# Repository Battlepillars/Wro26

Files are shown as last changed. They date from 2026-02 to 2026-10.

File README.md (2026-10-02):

<div align="left">

# Table of contents

<ul dir="auto">
    <li><details><summary><a href="#the-team">The team</a></summary>
        <ul dir="auto">
            <li><a href="#nils-stauff">Nils Stauff</a></li>
            <li><a href="#olivia-greilich">Olivia Greilich</a></li>
            <li><a href="#anton-wiesen">Anton Wiesen</a></li>
            <li><a href="#team-photo">Team photo</a></li>
        </ul>
        </details>
      </li>
    <li><a href="#videos-of-the-robot">Videos of the robot</a></li>
    <li><details><summary><a href="#mobility-and-mechanics">1. Mobility and mechanics</a></summary>
        <ul dir="auto">
            <li><a href="#development-goal">Development goal</a></li>
            <li><a href="#chassis-and-mechanical-structure">Chassis and mechanical structure</a>
              <ul dir="auto">
                <li><a href="#chassis-design">Chassis design</a></li>
                <li><a href="#base-deck-iteration">Base deck iteration</a></li>
                <li><a href="#chassis-structure">Chassis structure</a></li>
              </ul>
            </li>
            <li><a href="#drivetrain-concept-and-motor-selection">Drivetrain concept and motor selection</a></li>
            <li><a href="#rear-axle-and-differential">Rear axle and differential</a></li>
            <li><a href="#front-axle-and-steering">Front axle and steering</a>
              <ul dir="auto">
                <li><a href="#ackermann-condition-in-our-steering">Ackermann condition in our steering</a></li>
                <li><a href="#mechanical-precision-of-our-steering">Mechanical precision of our steering</a></li>
                <li><a href="#front-axle-rims-and-tires">Front axle rims and tires</a></li>
              </ul>
            </li>
            <li><a href="#servo-selection-and-position">Servo selection and position</a>
              <ul dir="auto">
                <li><a href="#servo-selection">Servo selection</a></li>
                <li><a href="#servo-position">Servo position</a></li>
              </ul>
            </li>
          </ul>
          </details>
        </li>
        <li><details><summary><a href="#power-and-sensors">2. Power and sensors</a></summary>
        <ul dir="auto">
            <li><a href="#concept">Concept</a></li>
            <li><a href="#electronics-setup">Electronics setup</a></li>
            <li><a href="#camera-use-of-the-camera-and-calibration">Camera: use of the camera and calibration</a>
              <ul dir="auto">
                <li><a href="#use-of-the-camera">Use of the camera</a></li>
                <li><a href="#further-development-rotating-camera-tower">Further development: rotating camera tower</a></li>
                <li><a href="#calibration-procedure">Calibration procedure</a></li>
              </ul>
            </li>
            <li><a href="#distance-sensors">Distance sensors</a>
                <ul dir="auto">
                    <li><a href="#selection-of-distance-sensors">Selection of distance sensors</a></li>
                    <li><a href="#sensor-evaluation">Sensor evaluation</a></li>
                    <li><a href="#sensor-placement-in-the-robot">Sensor placement in the robot</a></li>
                </ul>
            </li>
            <li><a href="#gyro">Gyro</a></li>
            <li><a href="#power-budget-power-supply-and-consumption">Power budget: power supply and consumption</a>
                <ul dir="auto">
                    <li><a href="#worst-case-peak-current-and-regulator-sizing">Worst-case peak current and regulator sizing</a></li>
                    <li><a href="#measured-total-power-requirement">Measured total power requirement</a></li>
                    <li><a href="#runtime-calculation">Runtime calculation</a></li>
                    <li><a href="#avoiding-deep-discharge">Avoiding deep discharge</a></li>
                    <li><a href="#voltage-supply-of-the-individual-components">Voltage supply of the individual components</a></li>
                    <li><a href="#failure-modes-in-sensors-and-power-supply">Failure modes in sensors and power supply</a></li>
                </ul>
            </li>
          </ul>
          </details>
        </li>
        <li><details><summary><a href="#software-development">3. Software development</a></summary>
        <ul dir="auto">
            <li><a href="#software-architecture">Software architecture</a></li>
            <li><a href="#threading-and-system-flow">Threading and system flow</a></li>
            <li><a href="#driving-primitives-in-drivecontrollerpy">Driving primitives in driveController.py</a></li>
            <li><a href="#opening-challenge-driving-strategy">Opening challenge driving strategy</a></li>
            <li><a href="#obstacle-challenge-driving-strategy---strategy-change">Obstacle challenge driving strategy - strategy change</a>
              <ul dir="auto">
                <li><a href="#old-strategy-scanning-while-driving">Old strategy: scanning while driving</a></li>
                <li><a href="#new-strategy-full-scan-fixed-route">New strategy: full scan, fixed route</a></li>
                <li><a href="#passing-two-obstacles-in-one-section">Passing two obstacles in one section</a></li>
                <li><a href="#parking-and-un-parking">Parking and un-parking</a></li>
              </ul>
            </li>
            <li><a href="#serial-communication-and-data-model">Serial communication and data model</a></li>
            <li><a href="#camera-processing">Camera processing</a>
              <ul dir="auto">
                <li><a href="#mask-pipeline">Mask pipeline</a></li>
              </ul>
            </li>
            <li><a href="#software-improvements">Software improvements</a></li>
          </ul>
          </details>
        </li>
        <li><details><summary><a href="#overall-robot-system-and-technical-decisions">4. Overall robot system and technical decisions</a></summary>
        <ul dir="auto">
            <li><a href="#design-constraints">Design constraints</a></li>
            <li><a href="#system-level-risks">System-level risks</a></li>
            <li><a href="#our-robot">Our robot</a></li>
            <li><a href="#technical-specifications">Technical specifications</a></li>
            <li><a href="#system-architecture">System architecture</a></li>
            <li><a href="#key-technical-decisions">Key technical decisions</a>
              <ul dir="auto">
                <li><a href="#raspberry-pi-vs-pure-microcontroller">Raspberry Pi vs. pure microcontroller</a></li>
                <li><a href="#raspberry-pi-5-vs-raspberry-pi-cm5">Raspberry Pi 5 vs. Raspberry Pi CM5</a></li>
                <li><a href="#lidar-vs-time-of-flight-sensors--control-paradigm">LiDAR vs. time-of-flight sensors / control paradigm</a></li>
                <li><a href="#camera-height-and-detection-strategy">Camera height and detection strategy</a></li>
                <li><a href="#chassis-material-pla-vs-ppa-cf">Chassis material: PLA vs. PPA-CF</a></li>
                <li><a href="#gyro-bno055-with-and-without-magnetometer-vs-bno086-without-magnetometer">Gyro: BNO055 with and without magnetometer vs. BNO086 without magnetometer</a></li>
                <li><a href="#rear-axle-ball-differential-vs-rigid-axle">Rear axle: ball differential vs. rigid axle</a></li>
                <li><a href="#tof-sensor-vl53l8cx-vs-tmf8828">ToF sensor: VL53L8CX vs. TMF8828</a></li>
              </ul>
            </li>
            <li><a href="#development-milestones">Development milestones</a></li>
          </ul>
          </details>
        </li>
        <li><details><summary><a href="#5-construction-guide">5. Construction guide</a></summary>
        <ul dir="auto">
            <li><a href="#assembly-overview">Assembly overview</a></li>
            <li><a href="#step-1-preparing-the-3d-printed-parts">Step 1: Preparing the 3D-printed parts</a></li>
            <li><a href="#step-2-lower-deck-assembly">Step 2: Lower deck assembly</a>
              <ul dir="auto">
                <li><a href="#21-drive-motor-and-rear-axle-bearings">2.1 Drive motor and rear-axle bearings</a></li>
                <li><a href="#22-front-axle--steering-knuckles">2.2 Front axle / steering knuckles</a></li>
                <li><a href="#23-rear-axle-front-wheels-and-steering-linkage">2.3 Rear axle, front wheels and steering linkage</a></li>
              </ul>
            </li>
            <li><a href="#step-3-middle-deck-assembly">Step 3: Middle deck assembly</a>
              <ul dir="auto">
                <li><a href="#31-support-bridge-and-middle-deck">3.1 Support bridge and middle deck</a></li>
                <li><a href="#32-mount-the-baseboard-and-connect-all-components">3.2 Mount the baseboard and connect all components</a></li>
              </ul>
            </li>
            <li><a href="#step-4-upper-deck--tof-sensors-and-rotating-camera-tower">Step 4: Upper deck – ToF sensors and rotating camera tower</a>
              <ul dir="auto">
                <li><a href="#41-mount-the-upper-deck">4.1 Mount the upper deck</a></li>
                <li><a href="#42-insert-the-distance-sensors">4.2 Insert the distance sensors</a></li>
                <li><a href="#43-mount-the-camera-tower-and-camera">4.3 Mount the camera tower and camera</a></li>
                <li><a href="#44-connect-the-camera-pan-servo">4.4 Connect the camera pan servo</a></li>
              </ul>
            </li>
            <li><a href="#step-5-wiring">Step 5: Wiring</a></li>
            <li><a href="#step-6-software-installation">Step 6: Software installation</a>
              <ul dir="auto">
                <li><a href="#61-prepare-raspberry-pi-os">6.1 Prepare Raspberry Pi OS</a></li>
                <li><a href="#62-install-python-libraries">6.2 Install Python libraries</a></li>
                <li><a href="#63-install-battlepillars-software">6.3 Install Battlepillars software</a></li>
                <li><a href="#64-build-compile-and-upload-to-the-controllers">6.4 Build, compile and upload to the controllers</a></li>
              </ul>
            </li>
          </ul>
          </details>
        </li>
</ul>

# **The team** 
<div align="center">
    <a href="img/teamname.jpg" target="_blank">
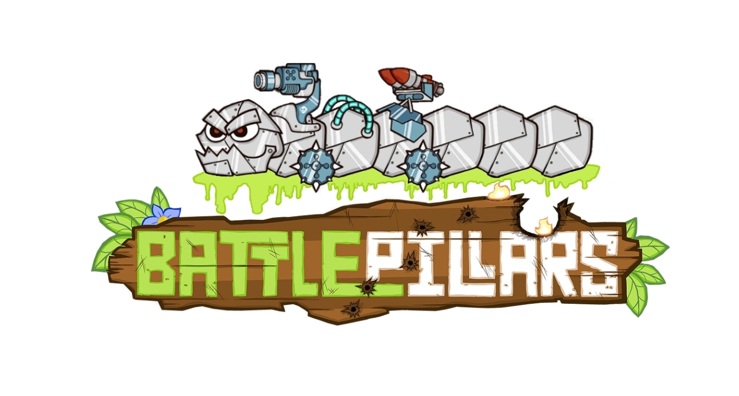
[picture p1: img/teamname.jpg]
        
    </a>
</div>
In this repository, you’ll find the documentation for the robot created by the "Battlepillars" for the 2026 World Robot Olympiad Future Engineers competition. The robot was the result of a collaborative effort by three students.

## **Nils Stauff**

<div align="center">
    <a href="img/nils.jpg" target="_blank">
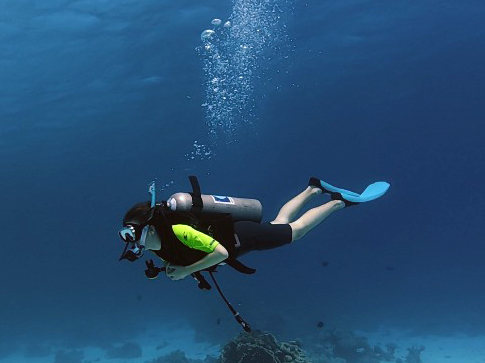
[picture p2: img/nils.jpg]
        
    </a>
</div>

Hi! I’m Nils, and I’m 17 years old. I enjoy coding and solving technical problems. In my free time, I like scuba diving and exploring the underwater world. During winter, I often go skiing, and I’m also a big fan of cats.

For our WRO project, I’m responsible for developing the robot’s software and making sure it runs as intended. It can be challenging at times, but it’s very rewarding when everything works as planned!

## **Olivia Greilich**

<div align="center">
    <a href="img/olivia.jpg" target="_blank">
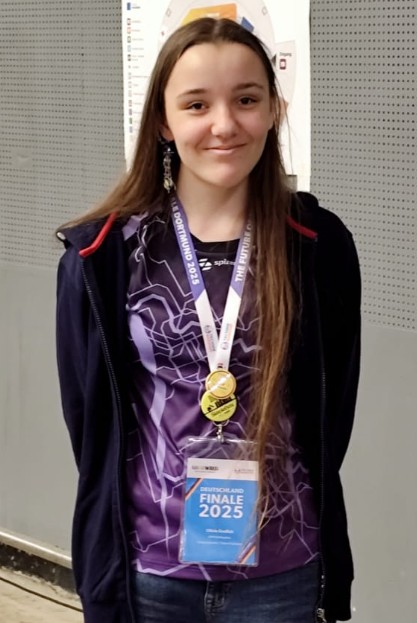
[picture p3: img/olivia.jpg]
        
    </a>
</div>

Hello everyone! My name is Olivia Greilich and I'm 17, currently attending the Lise-Meitner Gymnasium in Anrath. Languages, communicating and connecting with people is my passion, same with painting, sculpting and crocheting!
One interesting fact about me is that I am simply enamored with jellyfish of all types, colors, shapes and sizes. I have two jellyfish lamps, tons of stickers, books and of course a phone charm.
In my free time, I usually occupy myself with writing fanfiction on Archive Of Our Own (AO3).

My part of the team effort is the documentation and images you'll see below.

## **Anton Wiesen**

<div align="center">
    <a href="img/Einstellung_Lenkung.jpg" target="_blank">
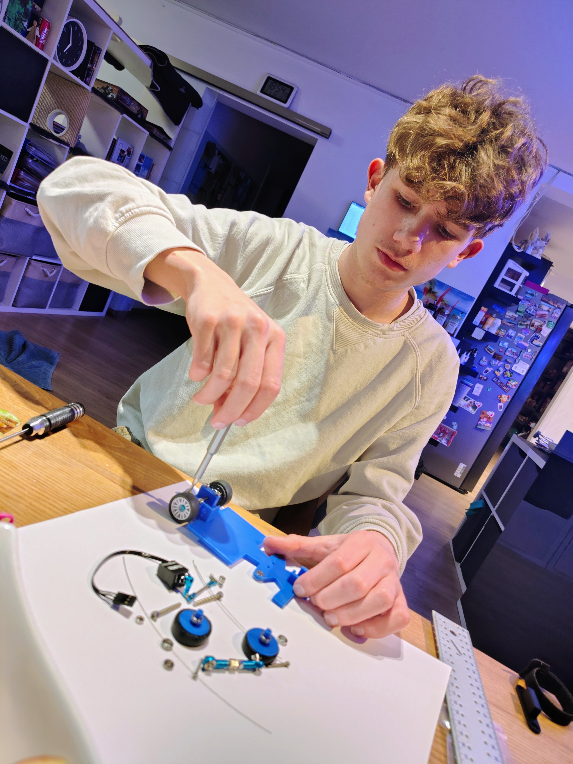
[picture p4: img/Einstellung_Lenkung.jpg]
        
    </a>
</div>

Hello! My name is Anton Wiesen, and I am 16 years old. I am responsible for the mechanical design of the robot and its technical components. My interests mainly lie in designing and building technology for robots. I am also quite experienced with 3D modelling software such as Fusion 360. In my free time, I like hanging out with friends and playing badminton at a sports club.

## **Team photo**

<div align="center">
    <a href="img/team.png" target="_blank">
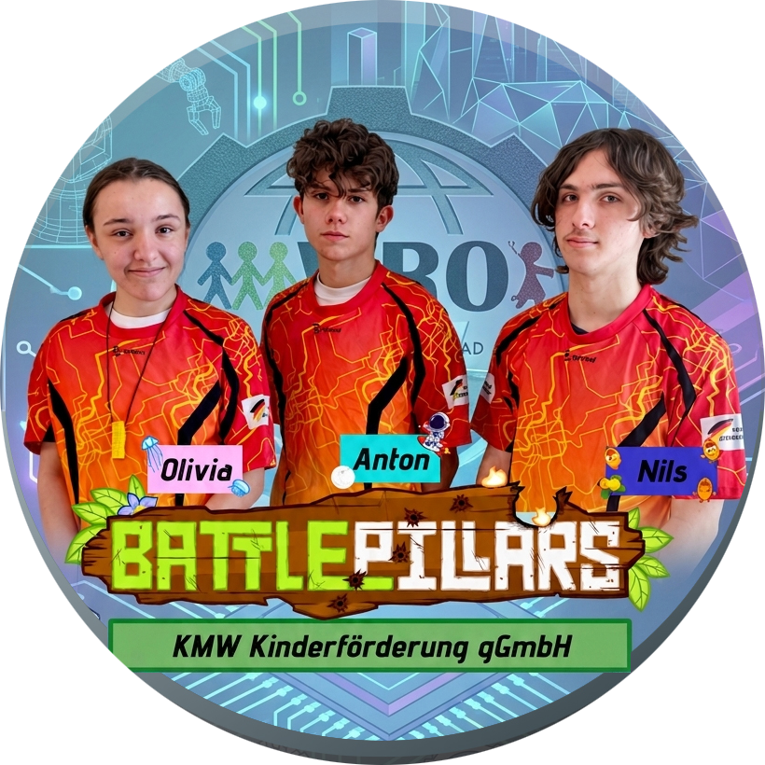
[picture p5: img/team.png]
        
    </a>
</div>
<br>

# **Videos of the robot**

The following videos show the vehicle operating autonomously, one video per run:

| Run | Link |
|---|---|
| Open Challenge | Open Challenge video (https://youtu.be/xgsjbz8JtRs?is=9g74XXmeAL3ZztfQ) |
| Obstacle Challenge | Obstacle Challenge video (https://youtu.be/dZyoW23Dgi8?is=IOlfB-I18UwgznLK) |

<br><br>

# **Mobility and mechanics**

## **Development goal**
In the 2025 season, we already successfully competed in the Future Engineers category and achieved the highest possible score in both runs at the World Final. 
<br><br>
**The goal for the 2026 season** was no longer just to reliably achieve the maximum score, but to complete the **course in the shortest possible time**. This led to three central mechanical development goals: a smaller and lighter chassis, a faster and more efficient drivetrain, and more precise steering. These goals led to a complete redesign of the chassis, drivetrain, front axle, and electronics layout.
<br><br>
The smaller form factor was meant to bring several advantages: the small size of the car allows for smaller turning radii and therefore higher agility. In addition, during the obstacle challenge, the car has more clearance to obstacles when passing through narrow sections, which makes driving more fault-tolerant and allows for higher speeds.

#### Figure 1: Comparison of the 2025 and 2026 robot designs:

<div align="center">
    <a href="img/vergleich_roboter.png" target="_blank">
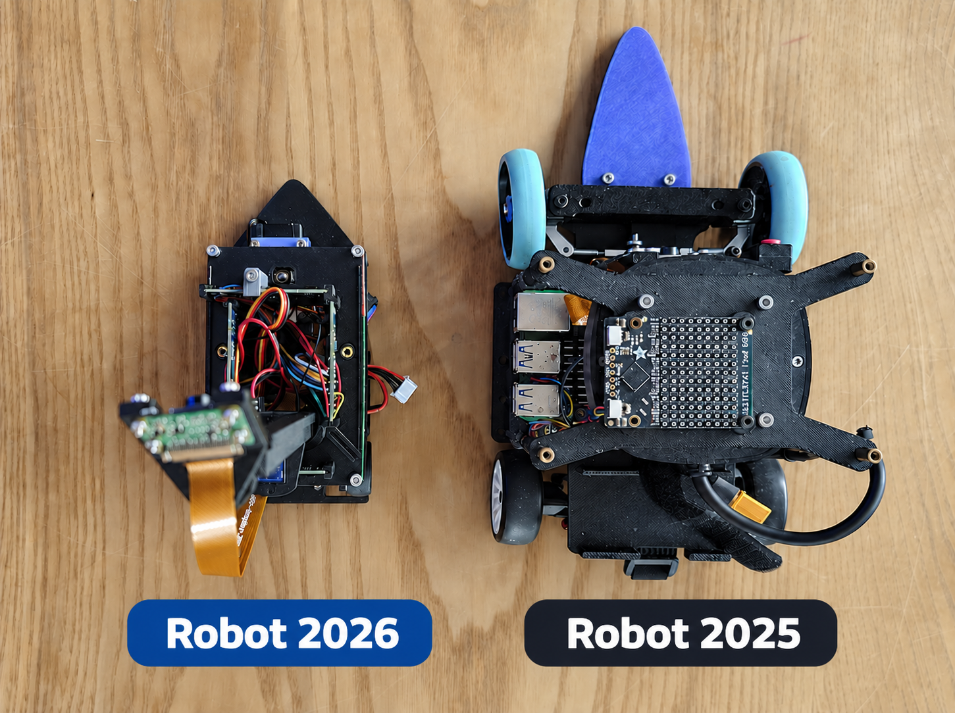
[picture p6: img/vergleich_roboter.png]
Comparison of the 2025 and 2026 robot designs
        
    </a>
</div>

<br>

## **Chassis and mechanical structure**

### **Chassis design**
The **chassis** was designed in Fusion 360. During development, **plain PLA** was used as filament since it is inexpensive and easy to print. However, the motor mount in PLA did not work reliably, since PLA creeps (deforms under constant pressure), which caused the gear backlash at the motor to drift out of tolerance.
<br><br>
In the final version, the chassis was manufactured from **PPA-CF filament**. PPA-CF is significantly stiffer and does not creep. As a result, the angles of the camera and sensors no longer change due to chassis flex. This improves the reproducibility of the sensor data and provides more consistent readings over the entire run.
<br><br>
However, this created a new problem. If the suspension was not exactly the same height on all sides, or the base deck was slightly warped, a wheel would hover slightly off the ground due to the extreme stiffness of the material and spin freely. In the previous PLA versions, this issue was compensated for by the springy properties of the material. Since we did not want to give up the positive properties of PPA-CF filament with respect to sensor data, we heated the base deck with a heat gun and carefully bent it until all wheels had good ground contact.

#### Table 1: Mechanical iterations in the chassis design:

<table align="center" border="1" style="border-collapse: collapse; border: 2px solid black; margin: 12px 0;">
  <tr>
    <th bgcolor="#4A90C2" style="border: 1px solid black; border-bottom: 3px solid black; padding: 8px; color: white;">Starting version</th>
    <th bgcolor="#4A90C2" style="border: 1px solid black; border-bottom: 3px solid black; padding: 8px; color: white;">Problem</th>
    <th bgcolor="#4A90C2" style="border: 1px solid black; border-bottom: 3px solid black; padding: 8px; color: white;">Observation before</th>
    <th bgcolor="#4A90C2" style="border: 1px solid black; border-bottom: 3px solid black; padding: 8px; color: white;">Change</th>
    <th bgcolor="#4A90C2" style="border: 1px solid black; border-bottom: 3px solid black; padding: 8px; color: white;">Observation after</th>
    <th bgcolor="#4A90C2" style="border: 1px solid black; border-bottom: 3px solid black; padding: 8px; color: white;">Decision</th>
  </tr>
  <tr>
    <td bgcolor="#EAF4FB" style="border: 1px solid black; padding: 8px;">Chassis made of PLA</td>
    <td bgcolor="#EAF4FB" style="border: 1px solid black; padding: 8px;">Motor mount deformed under continuous load, gear backlash drifted out of tolerance</td>
    <td bgcolor="#EAF4FB" style="border: 1px solid black; padding: 8px;">Backlash changed measurably after a few runs (creep), motor ran roughly</td>
    <td bgcolor="#EAF4FB" style="border: 1px solid black; padding: 8px;">Switched filament to PPA-CF</td>
    <td bgcolor="#EAF4FB" style="border: 1px solid black; padding: 8px;">Gear backlash constant, but new problem: wheel hovers slightly off the ground because base deck is too stiff</td>
    <td bgcolor="#EAF4FB" style="border: 1px solid black; padding: 8px;"><b>PPA-CF kept; new problem solved by manually rebending the base deck</b></td>
  </tr>
</table>
<br>

### **Base deck iteration**

At the start, the **base deck** consisted only of a simple rectangle. This first version served to roughly position the most important mechanical components and estimate the required footprint. The dimensions of the rear axle with ball differential, which we purchased as a pre-assembled unit with a fixed rear axle and wheel hubs, served as the initial reference point. This determined the wheelbase and thus the width of the base deck. The length of the base deck, on the other hand, was dictated by the dimensions of our self-developed PCB, since this was the largest component by area and was installed lengthwise in the chassis. For the rear axle we used a ball differential from the model-making sector, since a differential of this size is difficult to print reliably. The base deck was then gradually adapted to the actual mechanical requirements. During this process, more than fifteen versions of the base deck were created and printed until the final version was completed with all necessary cutouts, mounting points, and adaptations for the axles, wheels, sensors, and electronics. A total of ten ball bearings were used for the steering and suspension.

#### Figure 2: Iterations of the base deck:

<div align="center">
    <a href="img/iterationen_bodenplatte_eng.png" target="_blank">
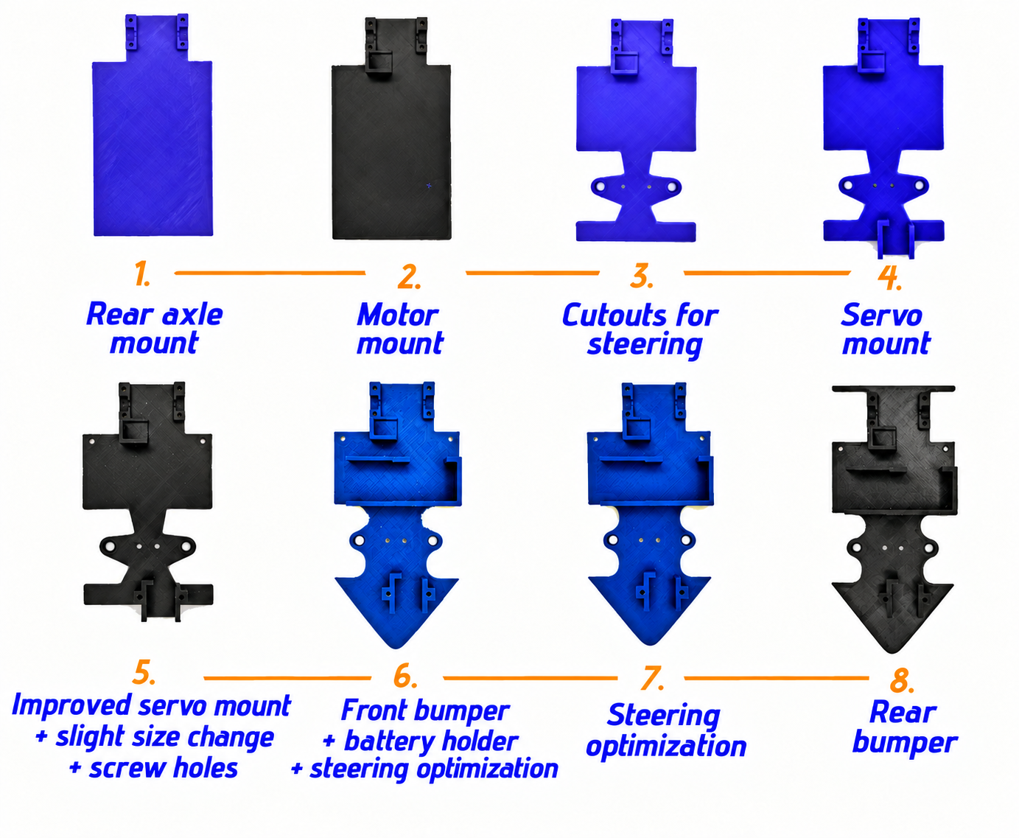
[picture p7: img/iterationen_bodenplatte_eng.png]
Iterations of the base deck
        
    </a>
</div>

### **Chassis structure**

The **chassis is split into three levels**, allowing a compact and clear integration of all components: 
<br>
<li>The base deck carries the drivetrain, battery, differential, and steering.</li>
<li>The middle deck houses the PCB, the Raspberry Pi CM5, the gyroscope, and the microcontroller.
<li>The top deck contains the camera and the ToF sensors.</li>
<br>

The finished vehicle with all components (PCB, battery, Raspberry Pi CM5, sensors, camera) has a **total weight of approx. 400 g**. 
<br>
#### Figure 3: Structure of the robot:

<div align="center">
    <a href="img/ebenen.jpg" target="_blank">
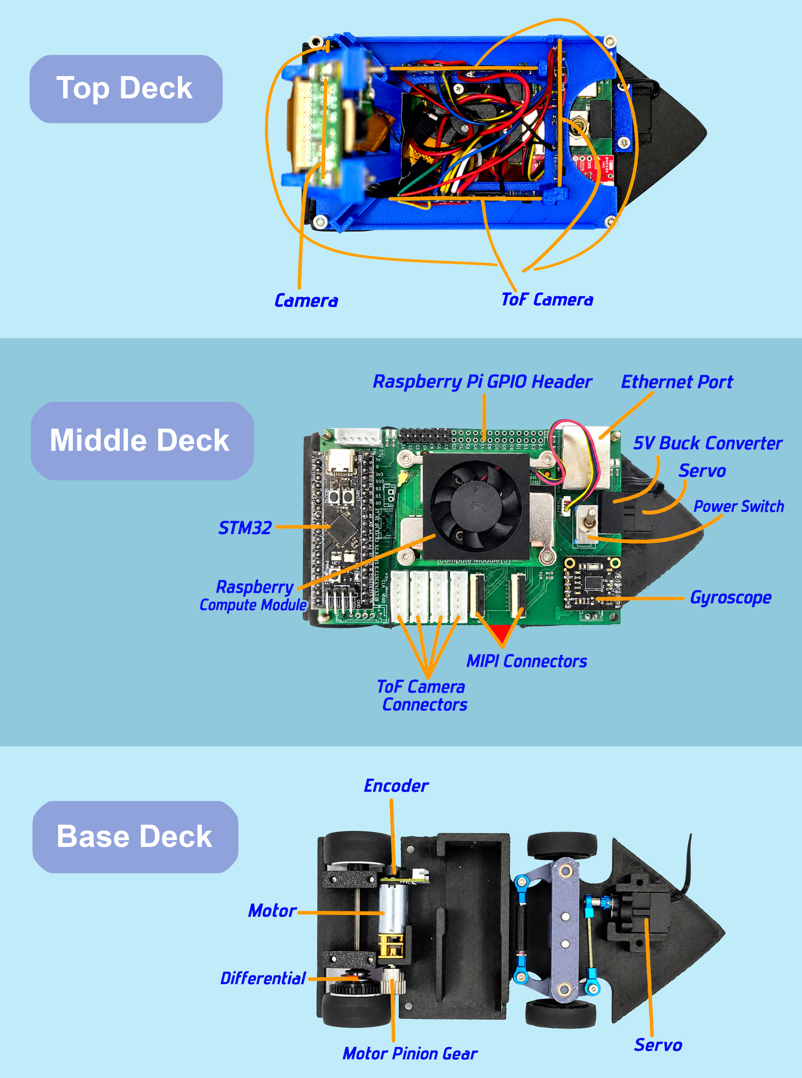
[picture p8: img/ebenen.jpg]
Three-level structure of the robot chassis
        
    </a>
</div>

## **Drivetrain concept and motor selection**

Our goal was to **drive one lap in about 10 seconds** – a race consists of three laps, which we therefore wanted to complete in about 30 seconds. The WRO track has a lap circumference (depending on the track layout) of about 8 m. This results in a required target speed of 8 m / 10 s = 0.8 m/s. However, we cannot drive at full speed permanently. Time is needed for acceleration and braking and for slower cornering. In addition, time is lost for parking and obstacle detection. These factors are hard to calculate, so we estimated a target speed of **2 m/s as the maximum speed** for our car.
<br><br>
Based on the chosen wheels (diameter approx. 27 mm, circumference approx. 84.8 mm), the wheel needs to complete about 23.7 revolutions per second (= 1410 RPM). To achieve the required wheel speed of about 1410 RPM, the gearbox output of the motor must deliver a **speed** of about 3384 RPM, due to the external gear ratio of 2.44:1. That is the first requirement for the motor.
<br><br>
The second requirement concerns **torque**. A motor must not only reach a high speed, but also deliver enough torque to reliably accelerate the vehicle under real conditions. We estimated the required torque based on the vehicle weight of approx. 450 g. Assuming a rolling friction coefficient of 0.05 and a wheel radius of 13.5 mm, this results in:
<br>
<table align="center" width="100%" cellpadding="8" cellspacing="0" border="0"><tr><td bgcolor="#B8D8EE" align="center">
Rolling resistance force: F<sub>roll</sub> = 0.45 kg × 9.81 m/s² × 0.05 ≈ 0.22 N<br>
Torque at the wheel: M<sub>wheel</sub> = 0.22 N × 0.0135 m ≈ 3.0 mNm
</td></tr></table>

Working backward through the external gear ratio, the motor must deliver at least 3.0 / 2.44 ≈ 1.2 mNm of torque, plus reserve for cornering and acceleration.

To find a suitable motor, we bought several small motors of the N20/N30 class that, according to their datasheets, promise high speeds at reasonable torque, and tested these directly in the vehicle. For this we wrote a **test program** that calculates the driving speed via the encoder on the motor. The STM32 reads a quadrature encoder and calculates the rotational speed. The encoder count is converted into a driving speed using the empirically calibrated factor: 

<table align="center" width="100%" cellpadding="8" cellspacing="0" border="0"><tr><td bgcolor="#B8D8EE" align="center">
v [m/s] = encoder count × 30 / (5.165 × 1000)</td></tr></table>

The factor 5.165 was determined from reference measurements over known distances.

 #### Table 2: Comparison of tested motors

<table align="center" border="1" style="border-collapse: collapse; border: 2px solid black;">

  <!-- Table header -->
  <tr>
    <th bgcolor="#4A90C2" width="120" style="border: 1px solid black; border-bottom: 3px solid black; padding: 8px; color: white;">Motor</th>
    <th bgcolor="#4A90C2" width="160" style="border: 1px solid black; border-bottom: 3px solid black; padding: 8px; color: white;">No-load speed<br>(datasheet)</th>
    <th bgcolor="#4A90C2" width="160" style="border: 1px solid black; border-bottom: 3px solid black; padding: 8px; color: white;">Rated torque<br>(datasheet)</th>
    <th bgcolor="#4A90C2" width="160" style="border: 1px solid black; border-bottom: 3px solid black; padding: 8px; color: white;">Measured<br>speed</th>
    <th bgcolor="#4A90C2" width="260" style="border: 1px solid black; border-bottom: 3px solid black; padding: 8px; color: white;">Observations</th>
    <th bgcolor="#4A90C2" width="120" style="border: 1px solid black; border-bottom: 3px solid black; padding: 8px; color: white;">Decision</th>
  </tr>

  <!-- N20 6V 600 rpm -->
  <tr>
    <td bgcolor="#EAF4FB" style="border: 1px solid black; padding: 8px;"><b>N20 6V<br>600 rpm</b></td>
    <td bgcolor="#EAF4FB" style="border: 1px solid black; padding: 8px; text-align: center;">600 rpm</td>
    <td bgcolor="#EAF4FB" style="border: 1px solid black; padding: 8px; text-align: center;">approx. 5 mNm</td>
    <td bgcolor="#EAF4FB" style="border: 1px solid black; padding: 8px; text-align: center;">approx. 0.7 m/s</td>
    <td bgcolor="#EAF4FB" style="border: 1px solid black; padding: 8px;">
      • too slow<br>
      • torque sufficient
    </td>
    <td bgcolor="#EAF4FB" style="border: 1px solid black; padding: 8px; text-align: center;">rejected</td>
  </tr>

  <!-- N20 6V 1500 rpm -->
  <tr>
    <td style="border: 1px solid black; padding: 8px;"><b>N20 6V<br>1500 rpm</b></td>
    <td style="border: 1px solid black; padding: 8px; text-align: center;">1500 rpm</td>
    <td style="border: 1px solid black; padding: 8px; text-align: center;">approx. 2 mNm</td>
    <td style="border: 1px solid black; padding: 8px; text-align: center;">approx. 1.5 m/s</td>
    <td style="border: 1px solid black; padding: 8px;">
      • motor gets very hot<br>
      • torque too low
    </td>
    <td style="border: 1px solid black; padding: 8px; text-align: center;">rejected</td>
  </tr>

  <!-- N30 6V 500 rpm -->
  <tr>
    <td bgcolor="#EAF4FB" style="border: 1px solid black; padding: 8px;"><b>N30 6V<br>500 rpm</b></td>
    <td bgcolor="#EAF4FB" style="border: 1px solid black; padding: 8px; text-align: center;">500 rpm</td>
    <td bgcolor="#EAF4FB" style="border: 1px solid black; padding: 8px; text-align: center;">approx. 9 mNm</td>
    <td bgcolor="#EAF4FB" style="border: 1px solid black; padding: 8px; text-align: center;">approx. 0.8 m/s</td>
    <td bgcolor="#EAF4FB" style="border: 1px solid black; padding: 8px;">
      • high torque<br>
      • speed too low
    </td>
    <td bgcolor="#EAF4FB" style="border: 1px solid black; padding: 8px; text-align: center;">rejected</td>
  </tr>

  <!-- N30 6V 1500 rpm – chosen motor -->
  <tr>
    <td style="border: 1px solid black; border-top: 3px solid black; padding: 8px;"><b>N30 6V<br>1500 rpm</b></td>
    <td style="border: 1px solid black; border-top: 3px solid black; padding: 8px; text-align: center;">1500 rpm</td>
    <td style="border: 1px solid black; border-top: 3px solid black; padding: 8px; text-align: center;">approx. 3 mNm</td>
    <td style="border: 1px solid black; border-top: 3px solid black; padding: 8px; text-align: center;"><b>approx. 2.1 m/s</b></td>
    <td style="border: 1px solid black; border-top: 3px solid black; padding: 8px;">
      • best speed
    </td>
    <td style="border: 1px solid black; border-top: 3px solid black; padding: 8px; text-align: center;"><b>used</b></td>
  </tr>

</table>

We chose the **N30 6V 1500 rpm**, since it achieved the highest real speed in the vehicle at approx. 2 m/s. Its rated torque of approx. 3 mNm is above the calculated minimum requirement of 1.2 mNm and provides sufficient reserve. According to the datasheet it reaches 1500 RPM at 6 V; scaled up to the operating voltage of 11.1 V (3S LiPo), this results in an extrapolated no-load speed of approx. 2775 RPM.  

## **Rear axle and differential**
#### Figure 4: Structure of the rear axle:
<div align="center">
    <a href="img/hinterachse.jpeg" target="_blank">
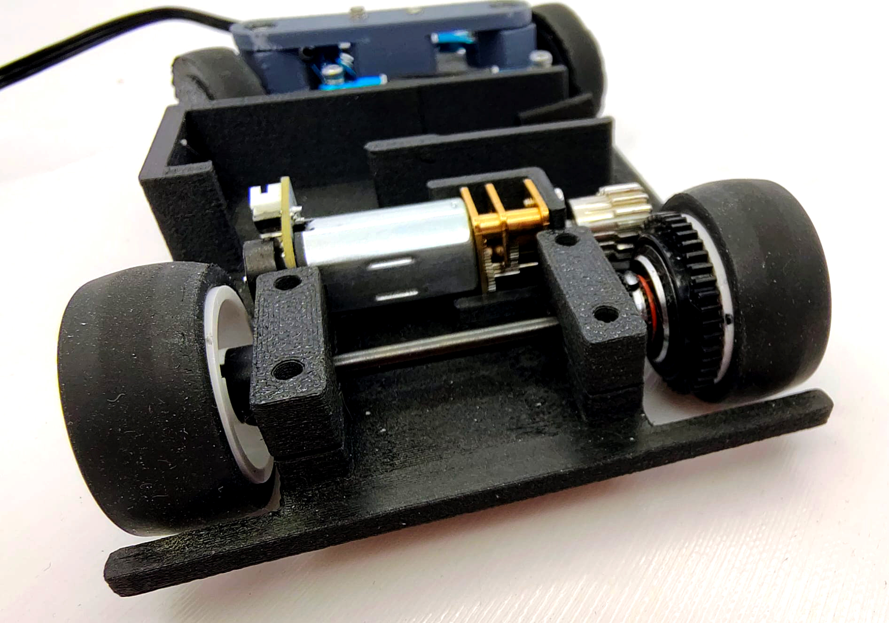
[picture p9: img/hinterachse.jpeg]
        
    </a>
</div>

The motor does not drive the rear wheels directly. Instead, we use a **ball differential** on the rear axle. This ball differential was procured as an assembly together with the corresponding Mini-Z wheel hubs and rear wheel rims. Therefore, we use the **Mini-Z rims** that belong to the system on the rear axle, since they are directly compatible with the differential without additional adapters. We use Mini-Z tires on all four wheels.

The N30 motor used is a geared motor with an internal ratio of 10:1. In addition, an external gear pair transmits the power to the rear axle: the drive pinion at the motor output has 18 teeth, the differential gear has 44 teeth, corresponding to a second ratio of 2.44:1. Both figures (10:1 and 2.44:1) are noted in the same power-flow direction motor → gearbox → axle. Overall, this results in a **total reduction** of about 24.4:1 (10:1 × 2.44:1) between the actual electric motor and the rear axle. 

The **rated torque** of the N30 motor is approx. 3 mNm according to the datasheet, after the internal ratio. This is a calculated, not a measured value: scaled up with the external ratio of 2.44:1, this results in an available torque of 3 mNm × 2.44 ≈ 7.3 mNm at the rear axle. 	

The **design** of the rear axle was carried out in Fusion 360 based on the ball differential. One challenge was that both the motor mount and the differential mount had to be manufactured mechanically precisely, so that the gear backlash between the motor pinion and the differential gear was correct. This was practically impossible to achieve by measuring and designing alone, since the dimensional accuracy of the printed parts was not high enough. So the correct distance was determined experimentally by changing the design parameters and reprinting the base deck until it fit. 

#### Table 3: Mechanical iterations in the rear axle design:

<table align="center" border="1" style="border-collapse: collapse; border: 2px solid black; margin: 12px 0;">
  <tr>
    <th bgcolor="#4A90C2" style="border: 1px solid black; border-bottom: 3px solid black; padding: 8px; color: white;">Starting version</th>
    <th bgcolor="#4A90C2" style="border: 1px solid black; border-bottom: 3px solid black; padding: 8px; color: white;">Problem</th>
    <th bgcolor="#4A90C2" style="border: 1px solid black; border-bottom: 3px solid black; padding: 8px; color: white;">Observation before</th>
    <th bgcolor="#4A90C2" style="border: 1px solid black; border-bottom: 3px solid black; padding: 8px; color: white;">Change</th>
    <th bgcolor="#4A90C2" style="border: 1px solid black; border-bottom: 3px solid black; padding: 8px; color: white;">Observation after</th>
    <th bgcolor="#4A90C2" style="border: 1px solid black; border-bottom: 3px solid black; padding: 8px; color: white;">Decision</th>
  </tr>
  <tr>
    <td bgcolor="#EAF4FB" style="border: 1px solid black; padding: 8px;">Calculated nominal distance, base deck version 1</td>
    <td bgcolor="#EAF4FB" style="border: 1px solid black; padding: 8px;">Gear backlash between motor pinion/differential could not be hit purely by calculation (print tolerances)</td>
    <td bgcolor="#EAF4FB" style="border: 1px solid black; padding: 8px;">Gearbox ran roughly, occasionally jammed/rattled</td>
    <td bgcolor="#EAF4FB" style="border: 1px solid black; padding: 8px;">Distance narrowed (1st tightening)</td>
    <td bgcolor="#EAF4FB" style="border: 1px solid black; padding: 8px;">Still rattling/backlash noticeable</td>
    <td bgcolor="#EAF4FB" style="border: 1px solid black; padding: 8px;">Narrow further</td>
  </tr>
  <tr>
    <td bgcolor="#EAF4FB" style="border: 1px solid black; padding: 8px;">Base deck after 1st tightening</td>
    <td bgcolor="#EAF4FB" style="border: 1px solid black; padding: 8px;">Backlash still too large</td>
    <td bgcolor="#EAF4FB" style="border: 1px solid black; padding: 8px;">Rattling reduced but still present</td>
    <td bgcolor="#EAF4FB" style="border: 1px solid black; padding: 8px;">Distance narrowed again (2nd tightening)</td>
    <td bgcolor="#EAF4FB" style="border: 1px solid black; padding: 8px;">Rattling nearly gone, but running slightly less smooth</td>
    <td bgcolor="#EAF4FB" style="border: 1px solid black; padding: 8px;">Narrow further</td>
  </tr>
  <tr>
    <td bgcolor="#EAF4FB" style="border: 1px solid black; padding: 8px;">Base deck after 2nd tightening</td>
    <td bgcolor="#EAF4FB" style="border: 1px solid black; padding: 8px;">Distance still not minimal enough</td>
    <td bgcolor="#EAF4FB" style="border: 1px solid black; padding: 8px;">Slight resistance in the gear mesh</td>
    <td bgcolor="#EAF4FB" style="border: 1px solid black; padding: 8px;">Distance narrowed a third time (3rd tightening)</td>
    <td bgcolor="#EAF4FB" style="border: 1px solid black; padding: 8px;">Gearbox now too tight, occasionally jammed/bound</td>
    <td bgcolor="#EAF4FB" style="border: 1px solid black; padding: 8px;">Widen again</td>
  </tr>
  <tr>
    <td bgcolor="#EAF4FB" style="border: 1px solid black; padding: 8px;">Base deck after 3rd tightening</td>
    <td bgcolor="#EAF4FB" style="border: 1px solid black; padding: 8px;">Distance too small, gearbox binding</td>
    <td bgcolor="#EAF4FB" style="border: 1px solid black; padding: 8px;">Gearbox occasionally jammed/bound</td>
    <td bgcolor="#EAF4FB" style="border: 1px solid black; padding: 8px;">Distance widened again slightly</td>
    <td bgcolor="#EAF4FB" style="border: 1px solid black; padding: 8px;">Quiet, smooth running without rattling/jamming</td>
    <td bgcolor="#EAF4FB" style="border: 1px solid black; padding: 8px;"><b>Final base-deck geometry adopted</b></td>
  </tr>
</table>

## **Front axle and steering**

### Ackermann condition in our steering
For the front axle, as in the previous year, we chose **Ackermann steering**. With simple parallel steering, both front wheels turn by the same angle – in corners this leads to lateral slip, because the inner wheel travels a smaller radius than the outer wheel and would therefore need to turn in more. Ackermann steering solves this problem by designing the steering geometry so that the extended wheel axes of both front wheels intersect at a common point on the extension of the rear axle. The ideal condition for this is:

<table align="center" width="100%" cellpadding="8" cellspacing="0" border="0"><tr><td bgcolor="#B8D8EE" align="center">cot(δ<sub>outer</sub>) − cot(δ<sub>inner</sub>) = track width t / wheelbase L</td></tr></table>

With our track width t = 65 mm and wheelbase L = 80 mm, this results in a **target value of t/L = 0.81.**

Since no suitable off-the-shelf parts were available for our compact form factor, we designed the entire front axle ourselves in Fusion 360 and tested various steering geometry variants via 3D printing. 

#### Figure 5: Adjusting the steering geometry:
<div align="center">
    <a href="img/Einstellung_Lenkung2.jpg" target="_blank">
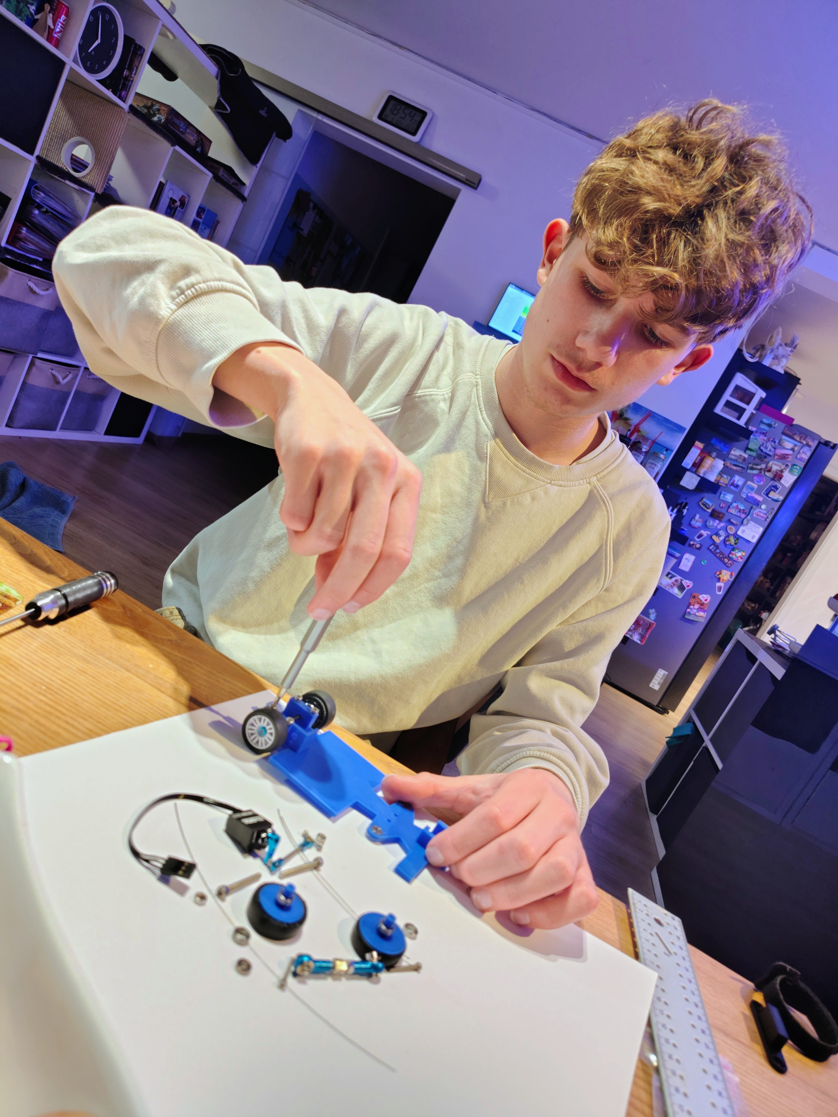
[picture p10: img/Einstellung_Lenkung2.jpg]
        
    </a>
</div>

#### Figure 6: Experimental validation of the Ackermann steering geometry using different steering angles and driving curves
<div align="center">
    <a href="img/ackermann_radien.jpg" target="_blank">
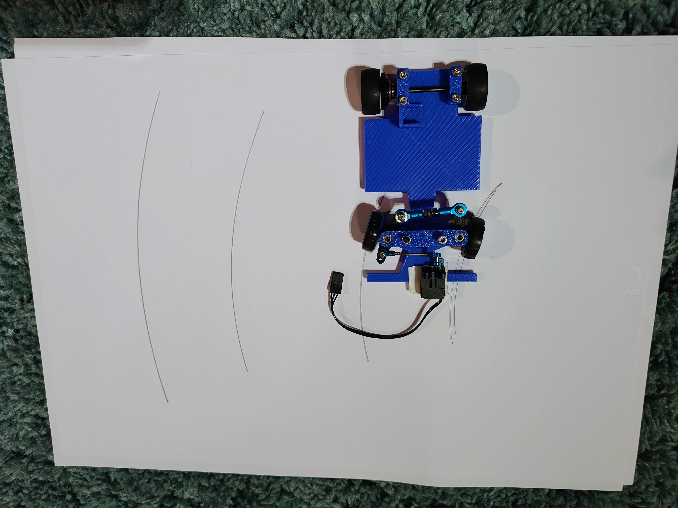
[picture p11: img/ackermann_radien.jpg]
        
    </a>
</div>

At maximum steering lock, the inner wheel reaches 45° and the outer wheel 35°, which gives:

<table align="center" width="100%" cellpadding="8" cellspacing="0" border="0"><tr><td bgcolor="#B8D8EE" align="center">
cot(35°) − cot(45°) = 1.43 − 1.00 = 0.43
</td></tr></table>

The achieved value of 0.43 is clearly below the ideal value of 0.81. With an unchanged outer angle of 35°, the inner wheel would theoretically need to reach about 58.5° to fully satisfy the Ackermann condition. However, this is not mechanically possible, since the inner wheel is already at its mechanical stop at 45° and a larger angle would exceed the available installation space. Alternatively, with an unchanged inner angle of 45°, the outer angle would need to be reduced to about 29°, which would reduce how sharply the car could turn. The steering therefore only partially satisfies the ideal Ackermann condition. As a result, the extended wheel axes of the front wheels do not intersect exactly at a common turning center, which can more easily cause lateral slip at the front wheels in tight corners:
#### Figure 7: Ackermann condition in our steering:
<div align="center">
    <a href="img/ackermann_englisch.png" target="_blank">
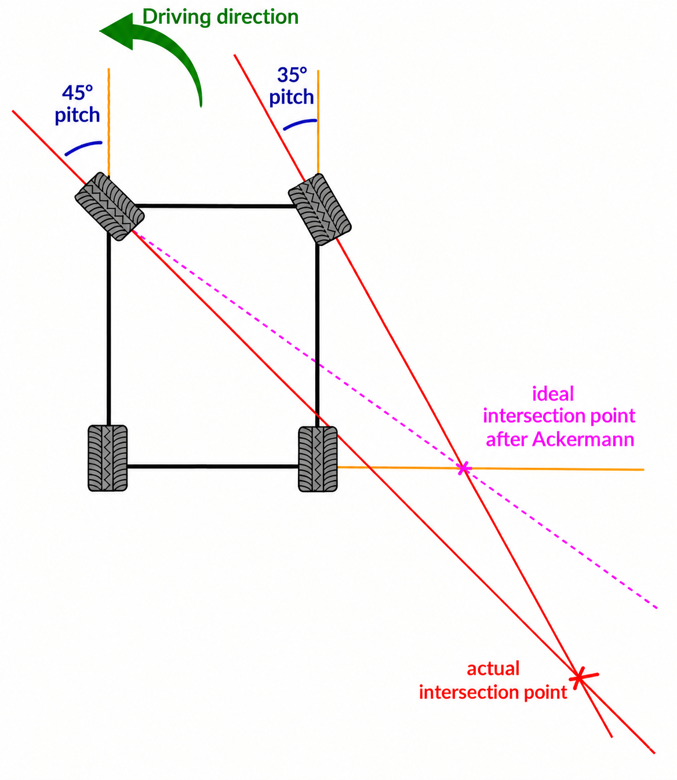
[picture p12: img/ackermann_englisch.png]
        
    </a>
</div>

The minimum turning radius (measured from the center of the rear axle to the center of the curve) is calculated as follows:

<table align="center" width="100%" cellpadding="8" cellspacing="0" border="0"><tr><td bgcolor="#B8D8EE" align="center">
Minimum turning radius = wheelbase / tan(δ<sub>outer</sub>)
</td></tr></table>

We had not set an exact target turning radius in advance, only the **requirement for the highest possible agility**. For reference: with the alternative possible outer angle of 29° (with an unchanged inner angle of 45°, see above), the minimum turning radius would have been 80 mm / tan(29°) ≈ 144 mm, compared to 114 mm with our actually chosen outer angle of 35°. Even 144 mm would still have been sufficient for the requirements of the WRO track, but would have noticeably reduced agility. We therefore deliberately chose the larger outer angle of 35° and thus decided against fully satisfying the Ackermann condition.

#### Table 4: Steering geometry trade-off – Ackermann compliance vs. agility:

<table align="center" border="1" style="border-collapse: collapse; border: 2px solid black; margin: 12px 0;">
  <tr>
    <th bgcolor="#4A90C2" style="border: 1px solid black; border-bottom: 3px solid black; padding: 8px; color: white;">Criterion</th>
    <th bgcolor="#4A90C2" style="border: 1px solid black; border-bottom: 3px solid black; padding: 8px; color: white;">Ideal Ackermann design</th>
    <th bgcolor="#4A90C2" style="border: 1px solid black; border-bottom: 3px solid black; padding: 8px; color: white;">Variant A:<br>optimal possible Ackermann compliance</th>
    <th bgcolor="#4A90C2" style="border: 1px solid black; border-bottom: 3px solid black; padding: 8px; color: white;">Variant B:<br>higher agility (chosen)</th>
  </tr>
  <tr>
    <td bgcolor="#EAF4FB" style="border: 1px solid black; padding: 8px;"><b>Outer angle δ<sub>outer</sub></b></td>
    <td bgcolor="#EAF4FB" style="border: 1px solid black; padding: 8px; text-align: center;">35°</td>
    <td bgcolor="#EAF4FB" style="border: 1px solid black; padding: 8px; text-align: center;">29°</td>
    <td style="border: 1px solid black; padding: 8px; text-align: center;"><b>35°</b></td>
  </tr>
  <tr>
    <td bgcolor="#EAF4FB" style="border: 1px solid black; padding: 8px;"><b>Inner angle δ<sub>inner</sub></b></td>
    <td bgcolor="#EAF4FB" style="border: 1px solid black; padding: 8px; text-align: center;">58.5°</td>
    <td bgcolor="#EAF4FB" style="border: 1px solid black; padding: 8px; text-align: center;">45° (mechanical cap)</td>
    <td style="border: 1px solid black; padding: 8px; text-align: center;"><b>45° (mechanical cap)</b></td>
  </tr>
  <tr>
    <td bgcolor="#EAF4FB" style="border: 1px solid black; padding: 8px;"><b>Ackermann figure<br>cot δ<sub>outer</sub> − cot δ<sub>inner</sub></b></td>
    <td bgcolor="#EAF4FB" style="border: 1px solid black; padding: 8px; text-align: center;">t/L = 0.81</td>
    <td bgcolor="#EAF4FB" style="border: 1px solid black; padding: 8px; text-align: center;">cot(29°) - cot(45°) = 0.80</td>
    <td style="border: 1px solid black; padding: 8px; text-align: center;"><b>0.43</b></td>
  </tr>
  <tr>
    <td bgcolor="#EAF4FB" style="border: 1px solid black; padding: 8px;"><b>Minimum turning radius</b></td>
    <td bgcolor="#EAF4FB" style="border: 1px solid black; padding: 8px; text-align: center;">n/a</td>
    <td bgcolor="#EAF4FB" style="border: 1px solid black; padding: 8px; text-align: center;">≈ 144 mm</td>
    <td style="border: 1px solid black; padding: 8px; text-align: center;"><b>≈ 114 mm</b></td>
  </tr>
  <tr>
    <td bgcolor="#EAF4FB" style="border: 1px solid black; padding: 8px;"><b>Agility</b></td>
    <td bgcolor="#EAF4FB" style="border: 1px solid black; padding: 8px; text-align: center;">n/a</td>
    <td bgcolor="#EAF4FB" style="border: 1px solid black; padding: 8px; text-align: center;">lower</td>
    <td style="border: 1px solid black; padding: 8px; text-align: center;"><b>higher</b></td>
  </tr>
  <tr>
    <td bgcolor="#EAF4FB" style="border: 1px solid black; border-top: 3px solid black; padding: 8px;"><b>Decision</b></td>
    <td bgcolor="#EAF4FB" style="border: 1px solid black; border-top: 3px solid black; padding: 8px; text-align: center;">not achievable by design</td>
    <td bgcolor="#EAF4FB" style="border: 1px solid black; border-top: 3px solid black; padding: 8px; text-align: center;">rejected</td>
    <td style="border: 1px solid black; border-top: 3px solid black; padding: 8px; text-align: center;"><b>chosen</b></td>
  </tr>
</table>

### Mechanical precision of our steering
However, in addition to the steering geometry, the **mechanical precision of the bearings** is also crucial for whether the calculated angles are actually reproducible during driving. Last year, our car only had one ball bearing per wheel. The steering knuckles were held in plain bearings. As a result, the wheels had noticeable lateral play (about 0.8 mm at the top edge of the wheel, see table) and wobbled back and forth. To minimize steering play, we used a total of eight ball bearings for the front axle bearings. Two per side support the steering knuckles, another two per side support the wheels. These ball bearings ensure precise steering with little play as well as low rolling resistance.

#### Table 5: Mechanical iterations in the front axle bearing:

<table align="center" border="1" style="border-collapse: collapse; border: 2px solid black; margin: 12px 0;">
  <tr>
    <th bgcolor="#4A90C2" style="border: 1px solid black; border-bottom: 3px solid black; padding: 8px; color: white;">Starting version</th>
    <th bgcolor="#4A90C2" style="border: 1px solid black; border-bottom: 3px solid black; padding: 8px; color: white;">Problem</th>
    <th bgcolor="#4A90C2" style="border: 1px solid black; border-bottom: 3px solid black; padding: 8px; color: white;">Measured value before</th>
    <th bgcolor="#4A90C2" style="border: 1px solid black; border-bottom: 3px solid black; padding: 8px; color: white;">Change</th>
    <th bgcolor="#4A90C2" style="border: 1px solid black; border-bottom: 3px solid black; padding: 8px; color: white;">Measured value after</th>
    <th bgcolor="#4A90C2" style="border: 1px solid black; border-bottom: 3px solid black; padding: 8px; color: white;">Decision</th>
  </tr>
  <tr>
    <td bgcolor="#EAF4FB" style="border: 1px solid black; padding: 8px;">Plain-bearing steering knuckles + 1 ball bearing/wheel (2025 season)</td>
    <td bgcolor="#EAF4FB" style="border: 1px solid black; padding: 8px;">Front wheels had lateral play, steering angle not reproducible while driving</td>
    <td bgcolor="#EAF4FB" style="border: 1px solid black; padding: 8px;">≈ 0.8 mm (corresponds to ≈ 2.5° tilt play)</td>
    <td bgcolor="#EAF4FB" style="border: 1px solid black; padding: 8px;">Switched to 8 ball bearings (2× steering knuckle + 2× wheel per side)</td>
    <td bgcolor="#EAF4FB" style="border: 1px solid black; padding: 8px;">&lt; 0.1 mm (no longer noticeable)</td>
    <td bgcolor="#EAF4FB" style="border: 1px solid black; padding: 8px;"><b>8-ball-bearing solution adopted</b></td>
  </tr>
</table>

<sub><b>Measurement method (lateral wheel play):</b> Vehicle fixed, wheel aligned straight. The wheel is pushed by hand (without tools) alternately inward and outward at the top edge until the noticeable play limit is reached. The total lateral deflection at the top edge of the wheel is measured with a caliper against a fixed reference point. The conversion to a tilt angle is done via the wheel radius (≈ 18 mm): angle = arctan(deflection / wheel radius). The average of n = 5 measurements is given.</sub>

#### Figure 8: Cross-section of the front axle (top: angled cut, bottom: straight cut):
<div align="center">
    <a href="img/schnitt schraeg.png" target="_blank">
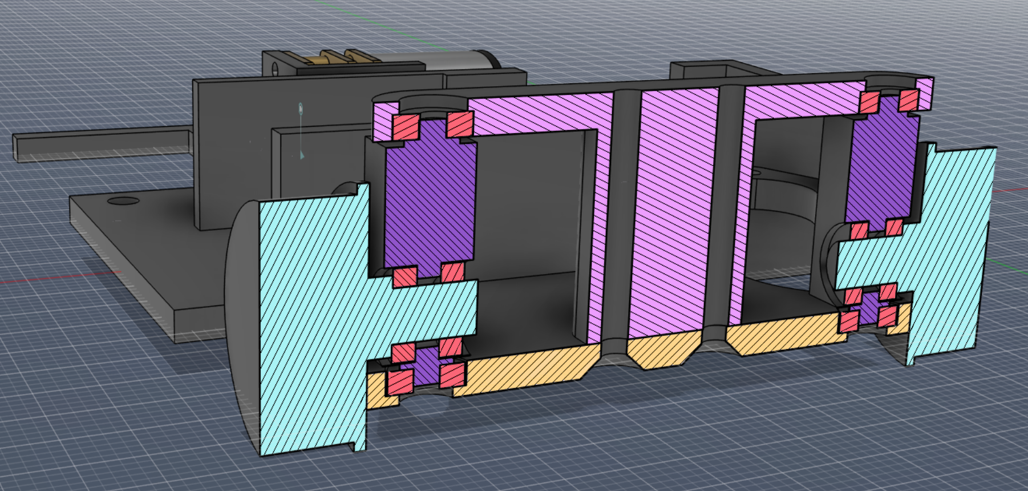
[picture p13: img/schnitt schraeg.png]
        
    </a>
    <br><sub>Angled cut: the four ball bearings per steering-knuckle side (marked in red) are visible, which support the steering knuckle (steering motion).</sub>
</div>
<br><br>
<div align="center">
    <a href="img/schnitt_gerade_eng.png" target="_blank">
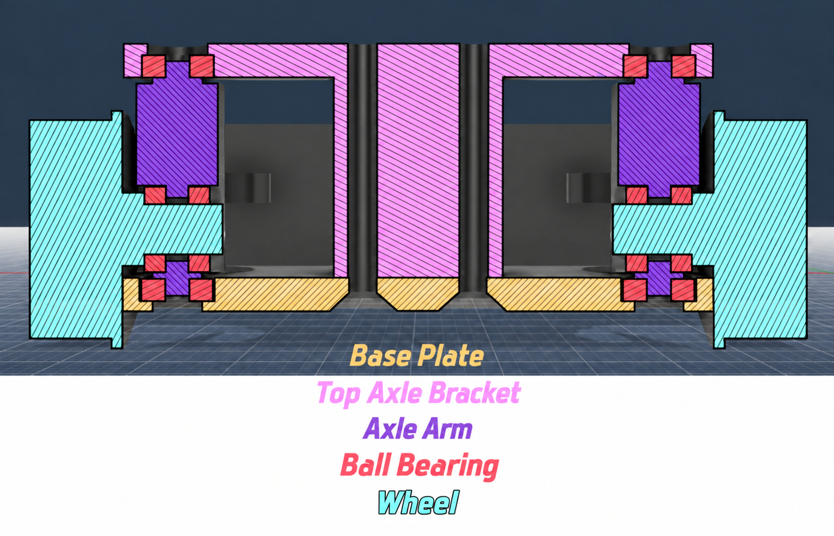
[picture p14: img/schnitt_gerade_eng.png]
      
    </a>
    <br><sub>Straight cut: the ball bearings of the wheel suspension (wheel axle) are visible, in addition to the steering-knuckle bearings in the left image.</sub>
</div>
<br>

### Front axle rims and tires
Since the front axle was fully designed by us, we do not use Mini-Z rims there, but **our own 3D-printed rims**. These were dimensioned so that the same Mini-Z tires used on the rear axle could be mounted on them. This means that all four wheels use the same tire type, while the rims are each adapted to the design of the front or rear axle respectively.

## **Servo selection and position**

### Servo selection
When **selecting** the steering servo, besides the size, quick availability was the main deciding factor. Initially, a particularly compact and inexpensive servo (approx. €2) with an all-plastic gearbox was used. However, the pronounced steering play of about 5° (measured, see table) proved insufficient for precise control, which is why the **INJORA N30 Nano** with a coreless motor, metal gearbox, and aluminum housing was chosen as a replacement. At 7 g and dimensions of 15.2 × 13.0 × 21.3 mm, it remains extremely compact; at 6 V it provides a torque of 1.3 kg·cm at an actuation speed of 0.05 s/60°. Since the force and reaction-time requirements in this application are low, almost any commercially available servo would have met the specification – the only decisive factor was the backlash-free metal gearbox.

#### Table 6: Mechanical iterations in the steering servo selection:

<table align="center" border="1" style="border-collapse: collapse; border: 2px solid black; margin: 12px 0;">
  <tr>
    <th bgcolor="#4A90C2" style="border: 1px solid black; border-bottom: 3px solid black; padding: 8px; color: white;">Starting version</th>
    <th bgcolor="#4A90C2" style="border: 1px solid black; border-bottom: 3px solid black; padding: 8px; color: white;">Problem</th>
    <th bgcolor="#4A90C2" style="border: 1px solid black; border-bottom: 3px solid black; padding: 8px; color: white;">Measured value before</th>
    <th bgcolor="#4A90C2" style="border: 1px solid black; border-bottom: 3px solid black; padding: 8px; color: white;">Change</th>
    <th bgcolor="#4A90C2" style="border: 1px solid black; border-bottom: 3px solid black; padding: 8px; color: white;">Measured value after</th>
    <th bgcolor="#4A90C2" style="border: 1px solid black; border-bottom: 3px solid black; padding: 8px; color: white;">Decision</th>
  </tr>
  <tr>
    <td bgcolor="#EAF4FB" style="border: 1px solid black; padding: 8px;">Compact servo with plastic gearbox (approx. €2)</td>
    <td bgcolor="#EAF4FB" style="border: 1px solid black; padding: 8px;">All-plastic gearbox showed noticeable steering play, leading to imprecise steering control</td>
    <td bgcolor="#EAF4FB" style="border: 1px solid black; padding: 8px;">≈ 5° (Δs ≈ 9 mm at r = 100 mm)</td>
    <td bgcolor="#EAF4FB" style="border: 1px solid black; padding: 8px;">Replaced with INJORA N30 Nano with metal gearbox</td>
    <td bgcolor="#EAF4FB" style="border: 1px solid black; padding: 8px;">≤ 1° (Δs ≤ 1.7 mm at r = 100 mm)</td>
    <td bgcolor="#EAF4FB" style="border: 1px solid black; padding: 8px;"><b>INJORA N30 Nano adopted</b></td>
  </tr>
</table>

<sub><b>Measurement method (steering play):</b> The servo is powered and actively holds the center position. A long, rigid pointer (e.g. a skewer, effective radius r = 100 mm) is attached to the steering arm/wheel. The wheel is pushed by hand with low force alternately in both directions until the noticeable play limit is reached, and the total lateral deflection Δs at the pointer tip is read against a fixed scale. The play angle results as angle = arctan(Δs / r). The average of n = 5 measurements is given.</sub>

### Servo position
The **positioning of the servo** presented an independent design challenge. The arrangement common in model vehicles – servo and linkage centered in the vehicle – was ruled out, because we needed a relatively short wheelbase for high agility and wanted to fit the battery between the front and rear wheels for a low center of gravity. After evaluating numerous configurations, the servo was moved in front of the front axle, with the linkage routed behind it. This allowed the bumper area to be used constructively without having to relocate the battery or the PCB; the center of gravity remained low and central, and the required steering lock was achieved without collisions.

<table width="100%" cellpadding="10" cellspacing="0" border="0"><tr><td bgcolor="#2E8B57" width="1%">&nbsp;</td><td bgcolor="#E2F3E5">
 <b>Result:</b> Ball-bearing front axle, metal-gear servo, and the new steering geometry together reduce the minimum turning radius from <b>172 mm to 114 mm</b> and eliminate noticeable steering play compared to the 2025 season.
</td></tr></table>

<br>

# **Power and sensors**

## **Concept**
To achieve the design goal of a small and fast vehicle, a fundamental overhaul of the electronics was necessary. The previous year's system used an RPLiDAR S2 for environment detection as well as two optical odometry sensors for position determination. Control was entirely coordinate-based – driving commands effectively read "go to coordinate X/Y". However, the LiDAR only provided ~10 updates per second with a delay of 100–200 ms, which meant position corrections only worked reliably while stationary. Odometry took over position tracking while driving, but limited the maximum speed to 0.5 m/s – above that, its measurements became unreliable.

For the new vehicle we therefore chose a fundamentally different approach: several **time-of-flight sensors** (VL53L8CX) continuously measure the distances to the walls at 30 Hz, enabling control without stopping. The control logic is now event-based – instead of "go to coordinate X/Y", a driving command now reads, for example, "drive toward the wall until the distance is 20 cm". Since no more stops are needed for position correction, the vehicle drives noticeably more smoothly and faster.

<table width="100%" cellpadding="10" cellspacing="0" border="0"><tr><td bgcolor="#2E8B57" width="1%">&nbsp;</td><td bgcolor="#E2F3E5">
 <b>Result:</b> The average time for a run in the obstacle challenge dropped from <b>160 s (2025)</b> to <b>35–45 s (2026)</b> – an improvement of about a factor of 4. The design goal of 30 s per run was thus narrowly missed.
</td></tr></table>
<br>

## **Electronics setup**

For the electronics, a test setup was first built on a **breadboard**. This allowed us to check whether the key components fundamentally worked before having our own PCB manufactured. Among other things, we tested the microcontroller, motor, motor encoder, motor driver, servo, time-of-flight sensors, and camera.

We developed the **PCB (baseboard)** ourselves using the open-source EDA tool **KiCad** (project files: <code>kicad/baseboard</code>). It is a two-layer PCB (2 copper layers) connected directly to the Raspberry Pi CM5 via a Hirose FH12-22S high-speed connector. It also carries the STM32F411, the voltage regulators, and the connectors for the motor, servo, gyroscope, and ToF sensors. The manufacturing files (Gerber data, bill of materials, position data) were exported with a KiCad fabrication-toolkit plugin (see <code>kicad/baseboard/production</code>); manufacturing and assembly were done externally. 

The complete electronics setup is shown in the wiring diagram below, which shows all connections between the baseboard, Raspberry Pi CM5, STM32, sensors, motor driver, and servo.

#### Figure 9: Wiring diagram

</div><div align="center">
    <a href="img/plan_gesamt%20Kopie.jpg" target="_blank">
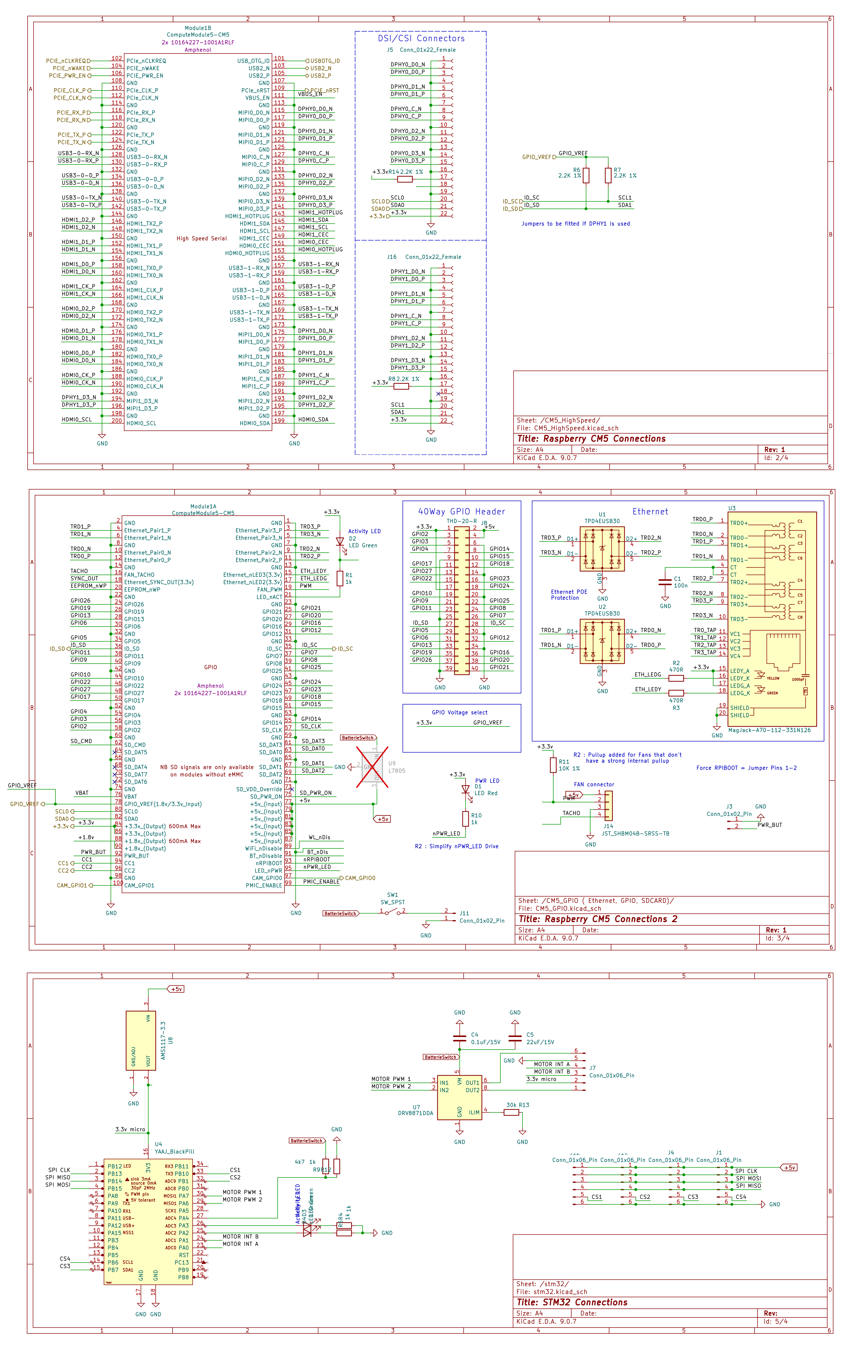
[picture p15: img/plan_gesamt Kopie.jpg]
        
    </a>
</div>

## **Camera: use of the camera and calibration**

### **Use of the camera** 
As in the previous year, we use the **Raspberry Pi Camera Module 3 Wide (12 MP)**, since it has proven itself.

Initially, the camera was mounted lower on the vehicle and the robot used a "scanning while driving" strategy. It drove to predefined positions and captured images of the course from there. However, reaching these positions took additional time and even small deviations in the robot's position could affect image recognition.

Three weeks before the regional competition in Germany, we therefore decided to mount the camera at a height of 27 cm – just below the maximum allowed height. From this position, the camera can see over the barriers and capture all relevant obstacles directly from the starting position.

This change – explained in detail later (cf. [Obstacle challenge driving strategy – strategy change](#obstacle-challenge-driving-strategy---strategy-change)) – enabled us to introduce a completely new full-scan strategy. Instead of scanning the course while driving, the robot now captures the required information before it starts moving. Based on this scan, the optimal route is calculated before the vehicle even sets off.

This approach makes obstacle detection considerably more demanding (cf. [mask pipeline](#mask-pipeline)), but simplifies the actual driving process significantly. Since the robot no longer needs to move to favorable camera positions during the run, valuable time can be saved.

<table width="100%" cellpadding="10" cellspacing="0" border="0"><tr><td bgcolor="#2E8B57" width="1%">&nbsp;</td><td bgcolor="#E2F3E5">
 <b>Result:</b> With the old <b>"scanning while driving"</b> strategy, we needed <b>56 s</b> on average per run, whereas the new <b>"full-scan strategy"</b> dropped this to only <b>38 s</b>.
</td></tr></table>

### **Further development: rotating camera tower**

Although the full-scan strategy significantly improved our driving time, the fixed camera still had limitations. A fixed viewing direction restricts the angles from which different areas of the course can be observed, making reliable obstacle detection more difficult in certain situations.

After the German national final in Trier, we therefore developed the system further for the **competition in Croatia**. Instead of using a fixed bracket, we mounted the **camera on a servo-driven, rotatable tower**.

The Raspberry Pi can now command the STM32 to rotate the tower to a specific angle (<code>setTowerAngle()</code> → <code>servo_tower</code> command). This allows the camera to be aimed precisely at different sections of the course instead of only looking straight ahead (cf. [Development milestones](#development-milestones)).

We expected this approach to improve the accuracy and reliability of obstacle detection, as the camera can actively select a suitable viewing angle for each relevant area rather than relying on a single fixed perspective.

<video src="https://github.com/Battlepillars/Wro26/raw/main/img/kamera_dreh.mp4" controls width="500"></video>

#### Video: First tests of the rotating camera

### **Calibration procedure**

The camera automatically calibrates its exposure time, white balance, and gain. Depending on the on-site lighting conditions, manual adjustments to the color masks in <code>cameraTower.py</code> may be necessary.

Before each competition run, we take a test image and check whether the obstacles are detected correctly. If they are not, we adjust the HSV values for the red and green masks. In OpenCV, the hue scale ranges from 0 to 179. Since red is the only color that appears at both ends of the scale, we create two separate masks to detect red and then combine them.

#### Table 7: HSV color masks and calibration parameters

<table align="center" border="1" style="border-collapse: collapse; border: 2px solid black;">

  <!-- Table header -->
  <tr>
    <th bgcolor="#4A90C2" width="120" style="border: 1px solid black; border-bottom: 3px solid black; padding: 8px; color: white;">Color</th>
    <th bgcolor="#4A90C2" width="140" style="border: 1px solid black; border-bottom: 3px solid black; padding: 8px; color: white;">H (min–max)</th>
    <th bgcolor="#4A90C2" width="140" style="border: 1px solid black; border-bottom: 3px solid black; padding: 8px; color: white;">S (min–max)</th>
    <th bgcolor="#4A90C2" width="140" style="border: 1px solid black; border-bottom: 3px solid black; padding: 8px; color: white;">V (min–max)</th>
    <th bgcolor="#4A90C2" width="400" style="border: 1px solid black; border-bottom: 3px solid black; padding: 8px; color: white;">Rationale</th>
  </tr>

  <!-- Red 1 -->
  <tr>
    <td bgcolor="#EAF4FB" style="border: 1px solid black; padding: 8px; text-align: center;"><b>Red 1</b></td>
    <td bgcolor="#EAF4FB" style="border: 1px solid black; padding: 8px; text-align: center;">0–10</td>
    <td bgcolor="#EAF4FB" style="border: 1px solid black; padding: 8px; text-align: center;">190–255</td>
    <td bgcolor="#EAF4FB" style="border: 1px solid black; padding: 8px; text-align: center;">190–255</td>
    <td bgcolor="#EAF4FB" style="border: 1px solid black; padding: 8px;">
      Rich, bright red (hue near 0°); high S and V thresholds filter out pale shades
    </td>
  </tr>

  <!-- Red 2 -->
  <tr>
    <td style="border: 1px solid black; padding: 8px; text-align: center;"><b>Red 2</b></td>
    <td style="border: 1px solid black; padding: 8px; text-align: center;">160–179</td>
    <td style="border: 1px solid black; padding: 8px; text-align: center;">100–255</td>
    <td style="border: 1px solid black; padding: 8px; text-align: center;">20–255</td>
    <td style="border: 1px solid black; padding: 8px;">
      Red at the upper hue end (wrap-around at 180°); wider S/V limits, since these red tones appear darker in the photo
    </td>
  </tr>

  <!-- Green -->
  <tr>
    <td bgcolor="#EAF4FB" style="border: 1px solid black; padding: 8px; text-align: center;"><b>Green</b></td>
    <td bgcolor="#EAF4FB" style="border: 1px solid black; padding: 8px; text-align: center;">35–95</td>
    <td bgcolor="#EAF4FB" style="border: 1px solid black; padding: 8px; text-align: center;">100–255</td>
    <td bgcolor="#EAF4FB" style="border: 1px solid black; padding: 8px; text-align: center;">20–255</td>
    <td bgcolor="#EAF4FB" style="border: 1px solid black; padding: 8px;">
      Wide range from yellow-green to blue-green; covers different lighting temperatures
    </td>
  </tr>

</table>

## **Distance sensors**

### **Selection of distance sensors**

For detecting the environment we use optical distance sensors, i.e. time-of-flight sensors. These measure the distance to objects optically. To make a concrete selection, we compared the datasheets of different sensors.

#### Table 8: Comparison of distance sensors

<table align="center" border="1" style="border-collapse: collapse; border: 2px solid black;">

  <!-- Table header -->
  <tr>
    <th bgcolor="#4A90C2" width="130" style="border: 1px solid black; border-bottom: 3px solid black; padding: 8px; color: white;">Sensor</th>
    <th bgcolor="#4A90C2" width="150" style="border: 1px solid black; border-bottom: 3px solid black; padding: 8px; color: white;">Manufacturer</th>
    <th bgcolor="#4A90C2" width="150" style="border: 1px solid black; border-bottom: 3px solid black; padding: 8px; color: white;">Zone<br>resolution</th>
    <th bgcolor="#4A90C2" width="130" style="border: 1px solid black; border-bottom: 3px solid black; padding: 8px; color: white;">FOV<br>(total)</th>
    <th bgcolor="#4A90C2" width="130" style="border: 1px solid black; border-bottom: 3px solid black; padding: 8px; color: white;">FOV/zone</th>
    <th bgcolor="#4A90C2" width="120" style="border: 1px solid black; border-bottom: 3px solid black; padding: 8px; color: white;">Max.<br>frequency</th>
    <th bgcolor="#4A90C2" width="130" style="border: 1px solid black; border-bottom: 3px solid black; padding: 8px; color: white;">Range</th>
    <th bgcolor="#4A90C2" width="140" style="border: 1px solid black; border-bottom: 3px solid black; padding: 8px; color: white;">Power<br>consumption</th>
    <th bgcolor="#4A90C2" width="130" style="border: 1px solid black; border-bottom: 3px solid black; padding: 8px; color: white;">Interface</th>
  </tr>

  <!-- VL53L9CX -->
  <tr>
    <td bgcolor="#EAF4FB" style="border: 1px solid black; padding: 8px; text-align: center;"><b>🟥 VL53L9CX<br>announced</b></td>
    <td bgcolor="#EAF4FB" style="border: 1px solid black; padding: 8px; text-align: center;">STMicro-<br>electronics</td>
    <td bgcolor="#EAF4FB" style="border: 1px solid black; padding: 8px; text-align: center;">54×42<br>(2268 zones)</td>
    <td bgcolor="#EAF4FB" style="border: 1px solid black; padding: 8px; text-align: center;">55°×42°<br>(71° diag.)</td>
    <td bgcolor="#EAF4FB" style="border: 1px solid black; padding: 8px; text-align: center;">🟩 ~1.0°<br>(per ST)</td>
    <td bgcolor="#EAF4FB" style="border: 1px solid black; padding: 8px; text-align: center;">🟩 100 Hz</td>
    <td bgcolor="#EAF4FB" style="border: 1px solid black; padding: 8px; text-align: center;">up to 880 cm</td>
    <td bgcolor="#EAF4FB" style="border: 1px solid black; padding: 8px; text-align: center;">~150 mW</td>
    <td bgcolor="#EAF4FB" style="border: 1px solid black; padding: 8px; text-align: center;">I3C /<br>MIPI CSI</td>
  </tr>

  <!-- VL53L1X -->
  <tr>
    <td style="border: 1px solid black; padding: 8px; text-align: center;"><b>VL53L1X</b></td>
    <td style="border: 1px solid black; padding: 8px; text-align: center;">STMicro-<br>electronics</td>
    <td style="border: 1px solid black; padding: 8px; text-align: center;">1 zone</td>
    <td style="border: 1px solid black; padding: 8px; text-align: center;">27°</td>
    <td style="border: 1px solid black; padding: 8px; text-align: center;">27°<br>(1 zone)</td>
    <td style="border: 1px solid black; padding: 8px; text-align: center;">50 Hz</td>
    <td style="border: 1px solid black; padding: 8px; text-align: center;">up to 400 cm</td>
    <td style="border: 1px solid black; padding: 8px; text-align: center;">~20 mW</td>
    <td style="border: 1px solid black; padding: 8px; text-align: center;">I²C</td>
  </tr>

  <!-- VL53L4CD -->
  <tr>
    <td bgcolor="#EAF4FB" style="border: 1px solid black; padding: 8px; text-align: center;"><b>VL53L4CD</b></td>
    <td bgcolor="#EAF4FB" style="border: 1px solid black; padding: 8px; text-align: center;">STMicro-<br>electronics</td>
    <td bgcolor="#EAF4FB" style="border: 1px solid black; padding: 8px; text-align: center;">1 zone</td>
    <td bgcolor="#EAF4FB" style="border: 1px solid black; padding: 8px; text-align: center;">18°<br>diagonal</td>
    <td bgcolor="#EAF4FB" style="border: 1px solid black; padding: 8px; text-align: center;">18°<br>(1 zone)</td>
    <td bgcolor="#EAF4FB" style="border: 1px solid black; padding: 8px; text-align: center;">100 Hz</td>
    <td bgcolor="#EAF4FB" style="border: 1px solid black; padding: 8px; text-align: center;">up to 120 cm</td>
    <td bgcolor="#EAF4FB" style="border: 1px solid black; padding: 8px; text-align: center;">0.15 mW<br>(ULP)</td>
    <td bgcolor="#EAF4FB" style="border: 1px solid black; padding: 8px; text-align: center;">I²C</td>
  </tr>

  <!-- TMF8828 -->
  <tr>
    <td style="border: 1px solid black; padding: 8px; text-align: center;"><b>🟨 TMF8828<br>close runner-up</b></td>
    <td style="border: 1px solid black; padding: 8px; text-align: center;">ams-OSRAM</td>
    <td style="border: 1px solid black; padding: 8px; text-align: center;">8×8<br>(64 zones)</td>
    <td style="border: 1px solid black; padding: 8px; text-align: center;">~45°<br>diagonal</td>
    <td style="border: 1px solid black; padding: 8px; text-align: center;">🟨 ~4.0°<br>(32°÷8)</td>
    <td style="border: 1px solid black; padding: 8px; text-align: center;">🟨 30 Hz</td>
    <td style="border: 1px solid black; padding: 8px; text-align: center;">up to 500 cm</td>
    <td style="border: 1px solid black; padding: 8px; text-align: center;">~75 mW</td>
    <td style="border: 1px solid black; padding: 8px; text-align: center;">I²C / SPI</td>
  </tr>

  <!-- TMF8821 -->
  <tr>
    <td bgcolor="#EAF4FB" style="border: 1px solid black; padding: 8px; text-align: center;"><b>TMF8821</b></td>
    <td bgcolor="#EAF4FB" style="border: 1px solid black; padding: 8px; text-align: center;">ams-OSRAM</td>
    <td bgcolor="#EAF4FB" style="border: 1px solid black; padding: 8px; text-align: center;">3×3<br>(9 zones)</td>
    <td bgcolor="#EAF4FB" style="border: 1px solid black; padding: 8px; text-align: center;">~41°<br>diagonal</td>
    <td bgcolor="#EAF4FB" style="border: 1px solid black; padding: 8px; text-align: center;">~9.7°<br>(29°÷3)</td>
    <td bgcolor="#EAF4FB" style="border: 1px solid black; padding: 8px; text-align: center;">30 Hz</td>
    <td bgcolor="#EAF4FB" style="border: 1px solid black; padding: 8px; text-align: center;">up to 500 cm</td>
    <td bgcolor="#EAF4FB" style="border: 1px solid black; padding: 8px; text-align: center;">~90 mW</td>
    <td bgcolor="#EAF4FB" style="border: 1px solid black; padding: 8px; text-align: center;">I²C / SPI</td>
  </tr>

  <!-- VL53L8CX -->
  <tr>
    <td style="border: 1px solid black; border-top: 3px solid black; padding: 8px; text-align: center;"><b>🟩 VL53L8CX<br>selected</b></td>
    <td style="border: 1px solid black; border-top: 3px solid black; padding: 8px; text-align: center;">STMicro-<br>electronics</td>
    <td style="border: 1px solid black; border-top: 3px solid black; padding: 8px; text-align: center;">8×8<br>(64 zones)</td>
    <td style="border: 1px solid black; border-top: 3px solid black; padding: 8px; text-align: center;">65°<br>diagonal</td>
    <td style="border: 1px solid black; border-top: 3px solid black; padding: 8px; text-align: center;">🟩 ~5.75°<br>(46°÷8)</td>
    <td style="border: 1px solid black; border-top: 3px solid black; padding: 8px; text-align: center;">🟩 60 Hz</td>
    <td style="border: 1px solid black; border-top: 3px solid black; padding: 8px; text-align: center;">up to 400 cm</td>
    <td style="border: 1px solid black; border-top: 3px solid black; padding: 8px; text-align: center;">~28 mW<br>(15 Hz, 8×8)</td>
    <td style="border: 1px solid black; border-top: 3px solid black; padding: 8px; text-align: center;">I²C / SPI</td>
  </tr>

</table>

A key criterion in sensor selection was that individual measurement zones should be as small as possible, so that walls can be distinguished from the floor at greater distances (FOV/zone in the table). The VL53L9CX would have been ideal due to its higher resolution, but was not yet available at the time of development. Between the VL53L8CX and the TMF8828, we chose the **VL53L8CX**, since its maximum measurement frequency according to the datasheet was significantly higher, and we expected faster obstacle-detection reaction times from it. In practice, however, it turned out that only ~30 Hz was achievable in 8×8 mode – meaning the TMF8828 might, in hindsight, have been the better choice. A sensor swap was no longer realistic at this point due to the advanced state of development.

### **Sensor evaluation**

The VL53L8CX offers **two operating modes**: in 4×4 mode it provides a measurement grid of 16 zones at a higher measurement frequency, while in 8×8 mode 64 zones are available at a lower frequency. To determine the mode suitable for our vehicle, we systematically tested both variants.

#### Figure 10: Test setup for sensor evaluation (distance measurement against a wall in defined steps)

</div><div align="center">
    <a href="img/Sensorpruefung (1).jpg" target="_blank">
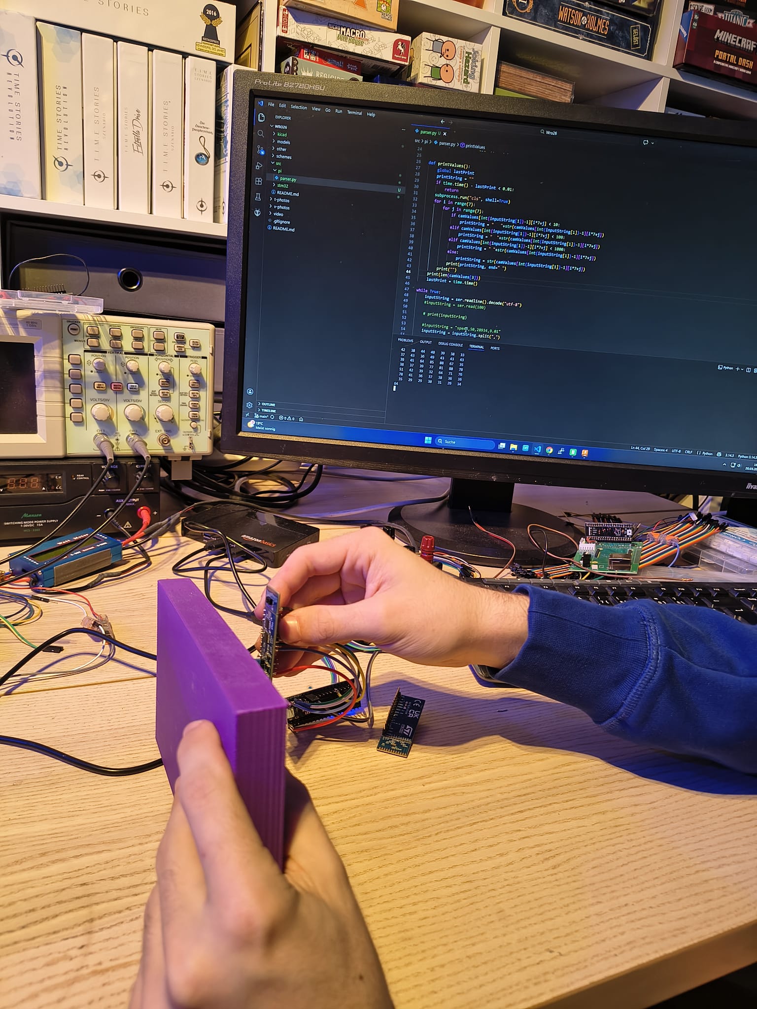
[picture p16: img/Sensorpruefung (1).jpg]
        
    </a>
</div>

One problem with **sensor placement** is the mounting height above the ground. If the sensor sits too low, individual measurement zones detect the floor instead of the wall, leading to measurement errors. If it sits too high, it can no longer reliably detect the lower edge of a wall. We tested various sensor heights and measured from which distance the wall is reliably detected and whether floor reflections disturb the measurement. 

Besides the height, we also investigated the influence of the measurement frequency on the maximum safe detection range. A higher frequency is beneficial for the driving strategy, since the STM32 receives updated distances more often and can react earlier. However, a higher frequency can lead to increased noise, which reduces the maximum reliable range. Table 9 summarizes the results.

#### Table 9: Detection reliability at different sensor heights 

<table align="center" border="1" style="border-collapse: collapse; border: 2px solid black;">

  <!-- Table header -->
  <tr>
    <th bgcolor="#4A90C2" width="160" style="border: 1px solid black; border-bottom: 3px solid black; padding: 8px; color: white;">Sensor height in mm</th>
    <th bgcolor="#4A90C2" width="170" style="border: 1px solid black; border-bottom: 3px solid black; padding: 8px; color: white;">Range 4×4<br>60 Hz in cm</th>
    <th bgcolor="#4A90C2" width="170" style="border: 1px solid black; border-bottom: 3px solid black; padding: 8px; color: white;">Range 4×4<br>30 Hz in cm</th>
    <th bgcolor="#4A90C2" width="170" style="border: 1px solid black; border-bottom: 3px solid black; padding: 8px; color: white;">Range 8×8<br>50 Hz in cm</th>
    <th bgcolor="#4A90C2" width="170" style="border: 1px solid black; border-bottom: 3px solid black; padding: 8px; color: white;">Range 8×8<br>30 Hz in cm</th>
  </tr>

  <!-- 30 mm -->
  <tr>
    <td bgcolor="#EAF4FB" style="border: 1px solid black; padding: 8px; text-align: center;">30</td>
    <td bgcolor="#EAF4FB" style="border: 1px solid black; padding: 8px; text-align: center;">40</td>
    <td bgcolor="#EAF4FB" style="border: 1px solid black; padding: 8px; text-align: center;">40</td>
    <td bgcolor="#EAF4FB" style="border: 1px solid black; padding: 8px; text-align: center;">40</td>
    <td bgcolor="#EAF4FB" style="border: 1px solid black; padding: 8px; text-align: center;">70</td>
  </tr>

  <!-- 40 mm -->
  <tr>
    <td style="border: 1px solid black; padding: 8px; text-align: center;">40</td>
    <td style="border: 1px solid black; padding: 8px; text-align: center;">50</td>
    <td style="border: 1px solid black; padding: 8px; text-align: center;">50</td>
    <td style="border: 1px solid black; padding: 8px; text-align: center;">40</td>
    <td style="border: 1px solid black; padding: 8px; text-align: center;">90</td>
  </tr>

  <!-- 50 mm -->
  <tr>
    <td bgcolor="#EAF4FB" style="border: 1px solid black; padding: 8px; text-align: center;">50</td>
    <td bgcolor="#EAF4FB" style="border: 1px solid black; padding: 8px; text-align: center;">60</td>
    <td bgcolor="#EAF4FB" style="border: 1px solid black; padding: 8px; text-align: center;">60</td>
    <td bgcolor="#EAF4FB" style="border: 1px solid black; padding: 8px; text-align: center;">50</td>
    <td bgcolor="#EAF4FB" style="border: 1px solid black; padding: 8px; text-align: center;">100</td>
  </tr>

  <!-- 60 mm -->
  <tr>
    <td style="border: 1px solid black; padding: 8px; text-align: center;"><b>🟩 60</b></td>
    <td style="border: 1px solid black; padding: 8px; text-align: center;">60</td>
    <td style="border: 1px solid black; padding: 8px; text-align: center;">60</td>
    <td style="border: 1px solid black; padding: 8px; text-align: center;">70</td>
    <td style="border: 1px solid black; padding: 8px; text-align: center;"><b>🟩 130</b></td>
  </tr>

  <!-- 70 mm -->
  <tr>
    <td bgcolor="#EAF4FB" style="border: 1px solid black; padding: 8px; text-align: center;">70</td>
    <td bgcolor="#EAF4FB" style="border: 1px solid black; padding: 8px; text-align: center;">60</td>
    <td bgcolor="#EAF4FB" style="border: 1px solid black; padding: 8px; text-align: center;">60</td>
    <td bgcolor="#EAF4FB" style="border: 1px solid black; padding: 8px; text-align: center;">70</td>
    <td bgcolor="#EAF4FB" style="border: 1px solid black; padding: 8px; text-align: center;">120</td>
  </tr>

  <!-- 80 mm -->
  <tr>
    <td style="border: 1px solid black; padding: 8px; text-align: center;">80</td>
    <td style="border: 1px solid black; padding: 8px; text-align: center;">60</td>
    <td style="border: 1px solid black; padding: 8px; text-align: center;">60</td>
    <td style="border: 1px solid black; padding: 8px; text-align: center;">60</td>
    <td style="border: 1px solid black; padding: 8px; text-align: center;">110</td>
  </tr>

  <!-- 90 mm -->
  <tr>
    <td bgcolor="#EAF4FB" style="border: 1px solid black; padding: 8px; text-align: center;">90</td>
    <td bgcolor="#EAF4FB" style="border: 1px solid black; padding: 8px; text-align: center;">50</td>
    <td bgcolor="#EAF4FB" style="border: 1px solid black; padding: 8px; text-align: center;">50</td>
    <td bgcolor="#EAF4FB" style="border: 1px solid black; padding: 8px; text-align: center;">60</td>
    <td bgcolor="#EAF4FB" style="border: 1px solid black; padding: 8px; text-align: center;">90</td>
  </tr>

</table>

Testing showed that although the 4x4 mode delivers a higher measurement frequency, it unfortunately only reliably detects narrow walls at a too-short distance. A single measurement point is then so large that it captures not only the wall but also the floor. That's why we chose the **8x8 mode at 30 Hz** and mounted the sensors at a **height of 60 mm**, since this achieved the greatest range (see table).

### **Sensor placement in the robot**
The time-of-flight sensors used have a **field of view of approx. 60°**. Originally, four sensors were planned.

#### Figure 11: Early version of the robot with four sensors

</div><div align="center">
    <a href="img/fruehe version roboter.jpg" target="_blank">
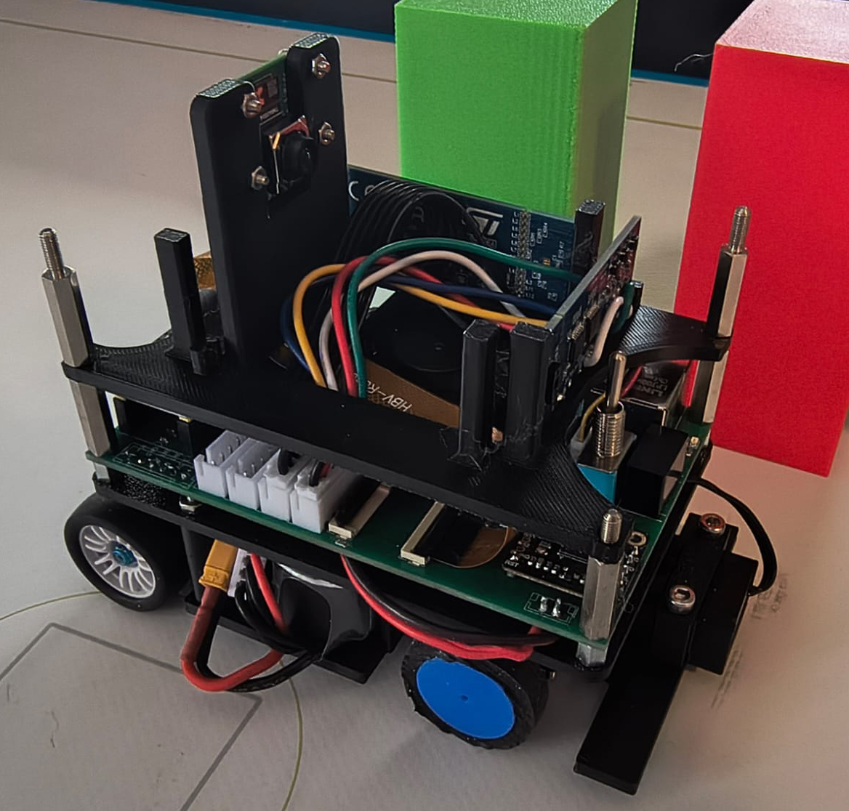
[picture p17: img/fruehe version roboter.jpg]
        
    </a>
</div>

However, driving tests revealed a problem: when approaching a wall at a 45° angle, a blind spot formed diagonally in front of the vehicle, since neither the front nor the side sensor sufficiently covered this area. 

#### Figure 12: Sensor coverage with four sensors

</div><div align="center">
    <a href="img/sensorabdeckung.png" target="_blank">
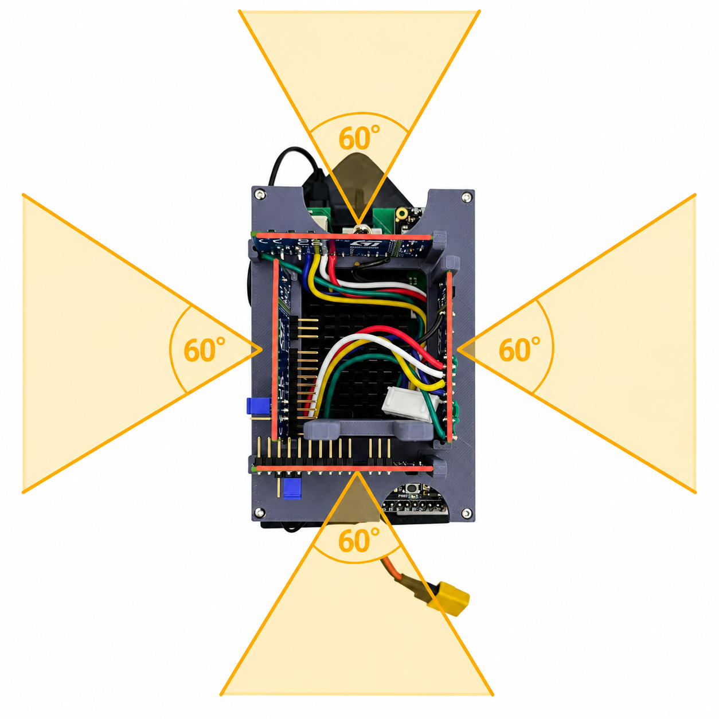
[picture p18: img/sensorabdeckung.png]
        
    </a>
</div>

To solve this problem, two additional sensors were added at the front, angled 45° forward. These were meant to detect walls earlier during diagonal approach. However, placing them at the front of the vehicle proved problematic, since the sensors blocked the camera's view, as the camera was not yet mounted at an elevated position at that time.

#### Figure 13: Coverage of the 45° blind spot by two additional sensors at the front

 </div><div align="center">
    <a href="img/sensorabdeckung_vorne.png" target="_blank">
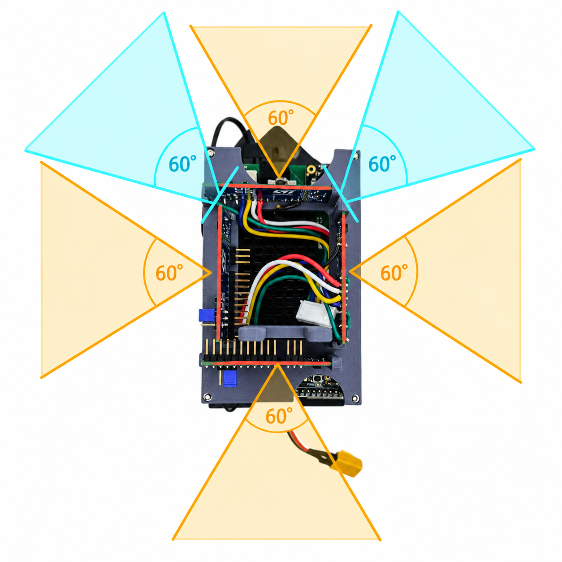
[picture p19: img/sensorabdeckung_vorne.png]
        
    </a>
</div>

 So we looked for an alternative solution. To save space, we switched to smaller PCBs that fit better mechanically into the compact chassis and installed them.

#### Figure 14: Size comparison of the sensor PCBs

 </div><div align="center">
    <a href="img/vergleich.jfif" target="_blank">
        
    </a>
</div>

#### Figure 15: Test position of an additional sensor angled forward diagonally

</div><div align="center">
    <a href="img/schraeg.jpg" target="_blank">
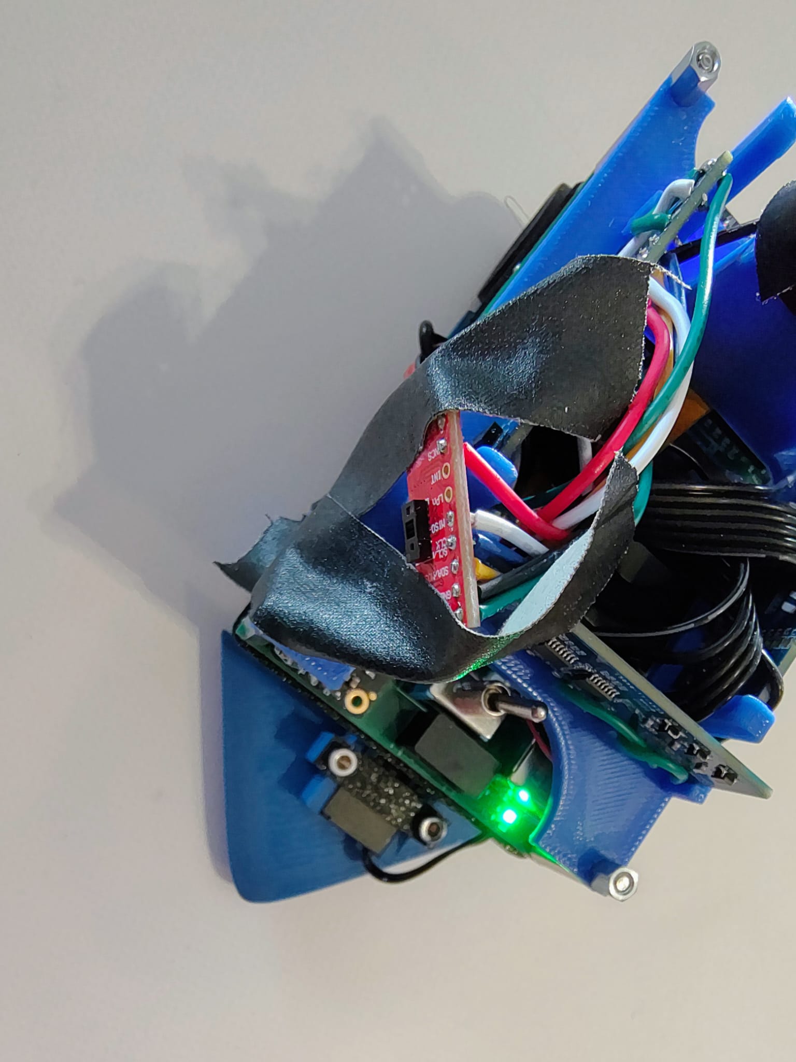
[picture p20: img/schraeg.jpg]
        
    </a>
</div>
 
 However, tests showed that this smaller variant did not work reliably enough – with more than two sensors, SPI communication broke down. 
We went back to the larger PCBs and instead placed them at the rear of the vehicle to keep the camera's view clear. Due to limited space, they were installed there in a vertical orientation. 

#### Figure 16: Position of the angled ToF sensors at the rear to cover the 45° blind spot

</div><div align="center">
    <a href="img/roboter spaetere version.jpg" target="_blank">
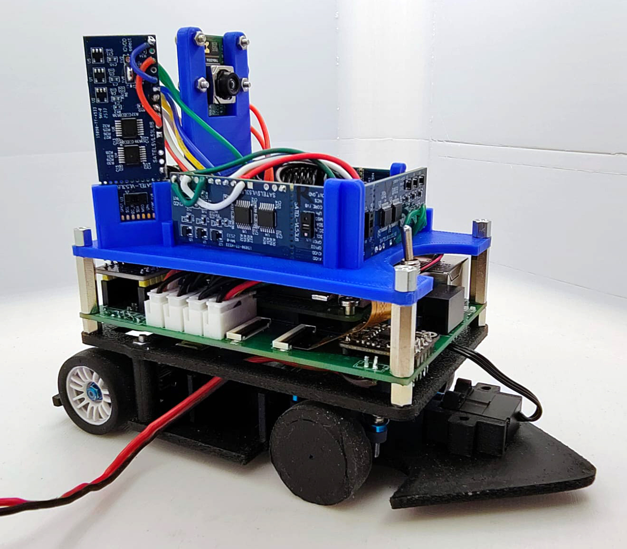
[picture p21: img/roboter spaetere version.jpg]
        
    </a>
</div>

#### Figure 17: Coverage of the 45° blind spot by two additional sensors at the rear

 </div><div align="center">
    <a href="img/sensorabdeckung_hinten.png" target="_blank">
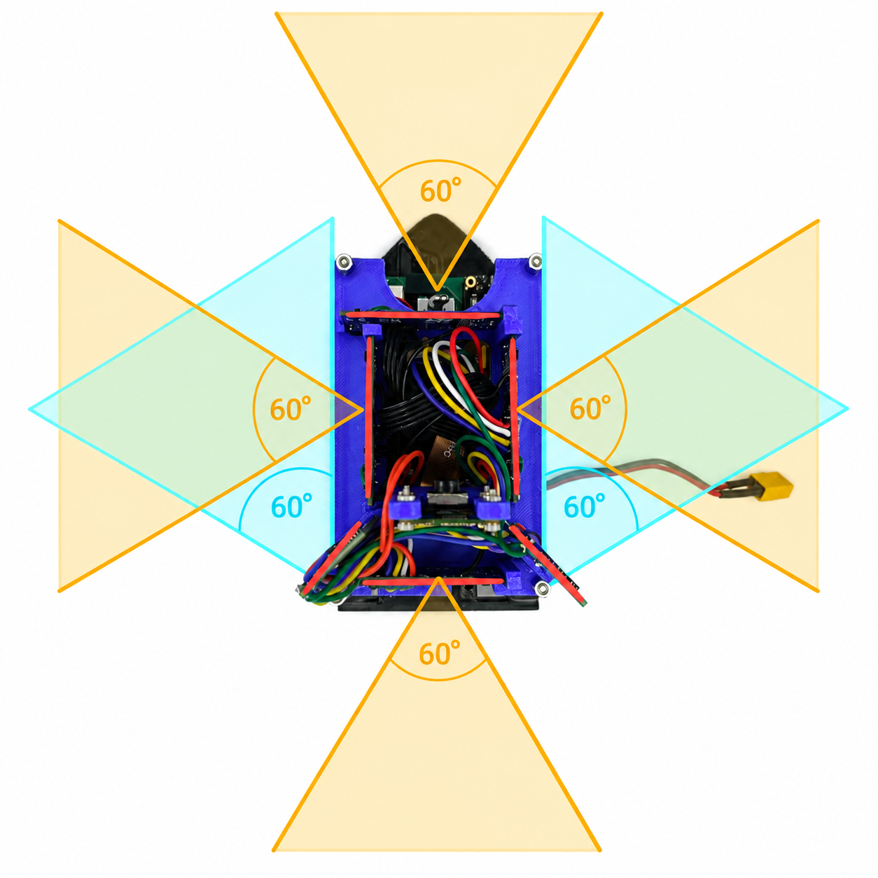
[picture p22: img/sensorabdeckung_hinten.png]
        
    </a>
</div>

After switching obstacle detection to a full scan (cf. [Camera](#camera-use-of-the-camera-and-calibration), [Obstacle challenge driving strategy – strategy change](#obstacle-challenge-driving-strategy---strategy-change)), we were able to do without the additional sensors. Since no favorable camera positions need to be approached anymore, the robot never approaches a wall at a 45° angle. 

#### Figure 18: Final robot with four sensors

</div><div align="center">
    <a href="img/endversion_tof.jpeg" target="_blank">
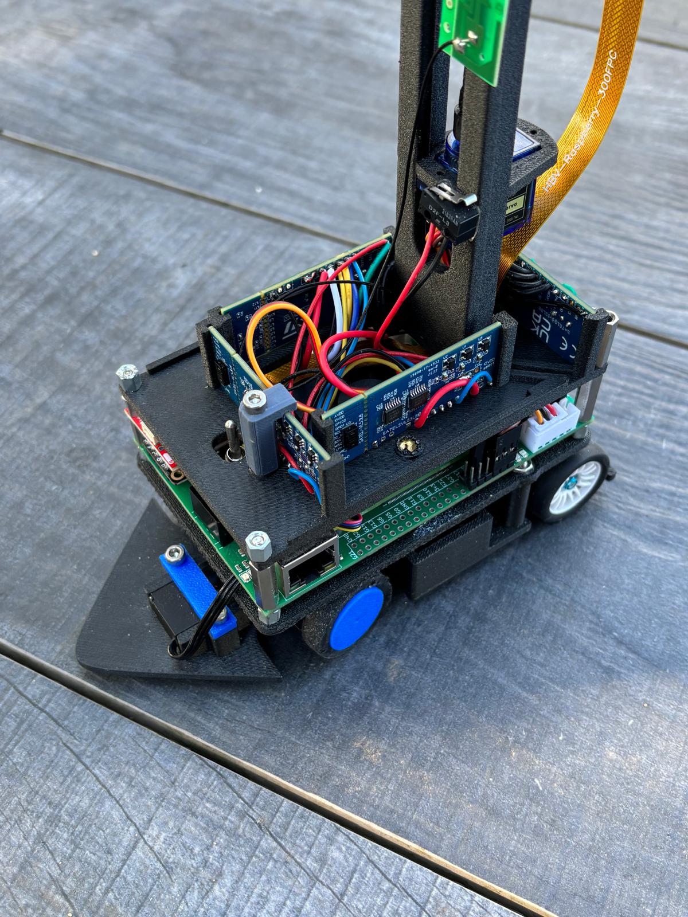
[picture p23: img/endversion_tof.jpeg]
        
    </a>
</div>

## **Gyro**
In the previous year, we had the problem that the **gyro** developed several degrees of drift over the course of a mission. This drift caused serious problems for the robot's orientation. This season we therefore wanted to use a **BNO055** with a built-in magnetometer. If the magnetometer works reliably, it can theoretically compensate for the drift completely. However, our tests showed that the magnetometer works far too imprecisely and unreliably. Deviations of 5–10 degrees occurred, which is why we had to disable it. With this limitation, the BNO055 performs even worse than last year's gyro. We had a deviation of about two degrees per lap driven, and about six degrees by the end of the course. The deviation is not constant across multiple runs, and therefore cannot be calibrated away. This makes navigation impossible. 

We therefore switched to a **BNO086** on short notice. We use this one without a magnetometer as well, but this gyro shows a significantly smaller and more consistent error. We perform a **bias calibration** (zero point of the rate sensors) automatically at program start; we determine the **rate calibration** manually by rotating the car ten times by 360 degrees. We then compare the measured and actual rotation and determine a correction factor. 

<table align="center" width="100%" cellpadding="8" cellspacing="0" border="0"><tr><td bgcolor="#B8D8EE" align="center">
Correction factor = measured rotation / expected rotation
</td></tr></table>

#### Table 10: Summary of gyro evaluation

<table align="center" border="1" style="border-collapse: collapse; border: 2px solid black;">

  <!-- Table header -->
  <tr>
    <th bgcolor="#4A90C2" width="130" style="border: 1px solid black; border-bottom: 3px solid black; padding: 8px; color: white;">Sensor</th>
    <th bgcolor="#4A90C2" width="220" style="border: 1px solid black; border-bottom: 3px solid black; padding: 8px; color: white;">Configuration</th>
    <th bgcolor="#4A90C2" width="150" style="border: 1px solid black; border-bottom: 3px solid black; padding: 8px; color: white;">Dev. after<br>1 lap</th>
    <th bgcolor="#4A90C2" width="170" style="border: 1px solid black; border-bottom: 3px solid black; padding: 8px; color: white;">Dev. after<br>3 laps</th>
    <th bgcolor="#4A90C2" width="170" style="border: 1px solid black; border-bottom: 3px solid black; padding: 8px; color: white;">Consistently<br>calibratable?</th>
  </tr>

  <!-- BNO055 with magnetometer -->
  <tr>
    <td bgcolor="#EAF4FB" style="border: 1px solid black; padding: 8px; text-align: center;"><b>BNO055</b></td>
    <td bgcolor="#EAF4FB" style="border: 1px solid black; padding: 8px;">with magnetometer</td>
    <td bgcolor="#EAF4FB" style="border: 1px solid black; padding: 8px; text-align: center;">~5–10°</td>
    <td bgcolor="#EAF4FB" style="border: 1px solid black; padding: 8px; text-align: center;">not measurable<br>(outlier)</td>
    <td bgcolor="#EAF4FB" style="border: 1px solid black; padding: 8px; text-align: center;">No</td>
  </tr>

  <!-- BNO055 without magnetometer -->
  <tr>
    <td style="border: 1px solid black; padding: 8px; text-align: center;"><b>BNO055</b></td>
    <td style="border: 1px solid black; padding: 8px;">without magnetometer</td>
    <td style="border: 1px solid black; padding: 8px; text-align: center;">~2°</td>
    <td style="border: 1px solid black; padding: 8px; text-align: center;">~6°</td>
    <td style="border: 1px solid black; padding: 8px; text-align: center;">No</td>
  </tr>

  <!-- BNO086 -->
  <tr>
    <td bgcolor="#EAF4FB" style="border: 1px solid black; padding: 8px; text-align: center;"><b>BNO086</b></td>
    <td bgcolor="#EAF4FB" style="border: 1px solid black; padding: 8px;">without magnetometer<br>with rate calibration</td>
    <td bgcolor="#EAF4FB" style="border: 1px solid black; padding: 8px; text-align: center;">~0.3°</td>
    <td bgcolor="#EAF4FB" style="border: 1px solid black; padding: 8px; text-align: center;">~1°</td>
    <td bgcolor="#EAF4FB" style="border: 1px solid black; padding: 8px; text-align: center;">Yes</td>
  </tr>

</table>

The table summarizes the results of our gyro evaluation. Each value is the average of five measured runs on our test course. The BNO086 was the only sensor for which the deviation was consistent across multiple runs and could therefore be compensated by our correction factor. In practice, it has been shown that the robot can still drive the course cleanly with this deviation.

<table width="100%" cellpadding="10" cellspacing="0" border="0"><tr><td bgcolor="#2E8B57" width="1%">&nbsp;</td><td bgcolor="#E2F3E5">
 <b>Result:</b> With the BNO086 and rate calibration, the gyro deviation is only about <b>1°</b> after three laps driven – precise enough to reliably drive the course.
</td></tr></table>

## **Power budget: power supply and consumption**
Last year we used a 2S 2200 mAh battery. This is far too large for our new car, and additionally the **voltage** is insufficient, since our new motor driver shuts off at 6.5 V. With line losses and under load spikes, reliable operation with a 2S battery as the battery voltage dropped was no longer possible during testing, so we switched to a 3S battery early on. This also gives us more power reserve for higher motor speeds. 

After voltage, the most important selection criterion was the **installation size** at the highest possible capacity. We chose a **3S LiPo battery with 550 mAh**. This is the largest battery we could fit in the chassis. To determine whether the battery was usable, we first calculated the runtime theoretically, then measured it in practice (see below).

#### Table 11: Power consumption of the components used, per datasheet

<table align="center" border="1" style="border-collapse: collapse; border: 2px solid black;">

  <!-- Table header -->
  <tr>
    <th bgcolor="#4A90C2" width="230" style="border: 1px solid black; border-bottom: 3px solid black; padding: 8px; color: white;">Component</th>
    <th bgcolor="#4A90C2" width="170" style="border: 1px solid black; border-bottom: 3px solid black; padding: 8px; color: white;">Operating voltage</th>
    <th bgcolor="#4A90C2" width="170" style="border: 1px solid black; border-bottom: 3px solid black; padding: 8px; color: white;">Typical current</th>
    <th bgcolor="#4A90C2" width="150" style="border: 1px solid black; border-bottom: 3px solid black; padding: 8px; color: white;">Typical<br>power</th>
    <th bgcolor="#4A90C2" width="380" style="border: 1px solid black; border-bottom: 3px solid black; padding: 8px; color: white;">Note</th>
  </tr>

  <!-- Raspberry Pi Compute Module 5 -->
  <tr>
    <td bgcolor="#EAF4FB" style="border: 1px solid black; padding: 8px;"><b>Raspberry Pi Compute Module 5</b></td>
    <td bgcolor="#EAF4FB" style="border: 1px solid black; padding: 8px; text-align: center;">5 V</td>
    <td bgcolor="#EAF4FB" style="border: 1px solid black; padding: 8px; text-align: center;">600–1600 mA</td>
    <td bgcolor="#EAF4FB" style="border: 1px solid black; padding: 8px; text-align: center;">3–8 W</td>
    <td bgcolor="#EAF4FB" style="border: 1px solid black; padding: 8px;">Main computer; depends on CPU load</td>
  </tr>

  <!-- Raspberry Pi Camera Module 3 -->
  <tr>
    <td style="border: 1px solid black; padding: 8px;"><b>Raspberry Pi Camera Module 3</b></td>
    <td style="border: 1px solid black; padding: 8px; text-align: center;">internal via CM5</td>
    <td style="border: 1px solid black; padding: 8px; text-align: center;">approx. 200–400 mA<br>equivalent</td>
    <td style="border: 1px solid black; padding: 8px; text-align: center;">approx. 1 W</td>
    <td style="border: 1px solid black; padding: 8px;">Powered directly via the CM5's MIPI CSI; no external power source</td>
  </tr>

  <!-- 4x VL53L8CX -->
  <tr>
    <td bgcolor="#EAF4FB" style="border: 1px solid black; padding: 8px;"><b>4× VL53L8CX time-of-flight sensor</b></td>
    <td bgcolor="#EAF4FB" style="border: 1px solid black; padding: 8px; text-align: center;">3.3 V (AVDD) via own voltage regulator</td>
    <td bgcolor="#EAF4FB" style="border: 1px solid black; padding: 8px; text-align: center;">approx. 85 mA each</td>
    <td bgcolor="#EAF4FB" style="border: 1px solid black; padding: 8px; text-align: center;">total<br>approx. 1.1 W</td>
    <td bgcolor="#EAF4FB" style="border: 1px solid black; padding: 8px;">Continuous operation 30 Hz, 8×8; per ST datasheet DS13349</td>
  </tr>

  <!-- BNO086 -->
  <tr>
    <td style="border: 1px solid black; padding: 8px;"><b>BNO086 IMU</b></td>
    <td style="border: 1px solid black; padding: 8px; text-align: center;">3.3 V</td>
    <td style="border: 1px solid black; padding: 8px; text-align: center;">approx. 4 mA</td>
    <td style="border: 1px solid black; padding: 8px; text-align: center;">approx. 13 mW</td>
    <td style="border: 1px solid black; padding: 8px;">Full fusion mode (NDOF); per manufacturer datasheet</td>
  </tr>

  <!-- STM32F411 -->
  <tr>
    <td bgcolor="#EAF4FB" style="border: 1px solid black; padding: 8px;"><b>STM32F411 Black Pill</b></td>
    <td bgcolor="#EAF4FB" style="border: 1px solid black; padding: 8px; text-align: center;">3.3 V</td>
    <td bgcolor="#EAF4FB" style="border: 1px solid black; padding: 8px; text-align: center;">approx. 45 mA</td>
    <td bgcolor="#EAF4FB" style="border: 1px solid black; padding: 8px; text-align: center;">approx. 150 mW</td>
    <td bgcolor="#EAF4FB" style="border: 1px solid black; padding: 8px;">100 MHz operation, all peripherals active; per ST DS10314</td>
  </tr>

  <!-- N30 Motor -->
  <tr>
    <td style="border: 1px solid black; padding: 8px;"><b>N30 motor with encoder</b></td>
    <td style="border: 1px solid black; padding: 8px; text-align: center;">11.1 V via DRV8871</td>
    <td style="border: 1px solid black; padding: 8px; text-align: center;">50–200 mA</td>
    <td style="border: 1px solid black; padding: 8px; text-align: center;">0.5–2 W</td>
    <td style="border: 1px solid black; padding: 8px;">Strongly load-dependent; peak current on start-up</td>
  </tr>

  <!-- DRV8871 -->
  <tr>
    <td bgcolor="#EAF4FB" style="border: 1px solid black; padding: 8px;"><b>DRV8871 motor driver</b></td>
    <td bgcolor="#EAF4FB" style="border: 1px solid black; padding: 8px; text-align: center;">11.1 V</td>
    <td bgcolor="#EAF4FB" style="border: 1px solid black; padding: 8px; text-align: center;">quiescent current<br>approx. 5 mA</td>
    <td bgcolor="#EAF4FB" style="border: 1px solid black; padding: 8px; text-align: center;">approx. 55 mW</td>
    <td bgcolor="#EAF4FB" style="border: 1px solid black; padding: 8px;">H-bridge, 6.5–45 V, max. 3.6 A; motor current flows directly through the driver</td>
  </tr>

  <!-- Servo -->
  <tr>
    <td style="border: 1px solid black; padding: 8px;"><b>Servo (steering)</b></td>
    <td style="border: 1px solid black; padding: 8px; text-align: center;">5 V</td>
    <td style="border: 1px solid black; padding: 8px; text-align: center;">150–800 mA<br>briefly</td>
    <td style="border: 1px solid black; padding: 8px; text-align: center;">0.5–2 W<br>briefly</td>
    <td style="border: 1px solid black; padding: 8px;">Current spikes during steering movements; low quiescent current</td>
  </tr>

</table>

### **Worst-case peak current and regulator sizing**
In addition to the typical values from Table 11, the **worst case** is decisive for sizing the voltage regulators, in which several consumers draw their peak current simultaneously on the 5 V rail:

- Raspberry Pi CM5 (peak load): 1600 mA
- Camera (powered internally via CM5, conservatively added here as well): 400 mA
- Servo (steering movement, briefly): 800 mA
- 4× VL53L8CX ToF sensors: 4 × 85 mA = 340 mA
- STM32F411 + BNO086 via AMS1117-3.3 (input current of the linear regulator comes from the 5 V rail): approx. 50 mA

**Worst-case peak current on the 5 V rail: ≈ 3.2 A**

On the 5 V rail we use an **AP3441SHE-7B** synchronous buck regulator (Diodes Inc., rated current 3 A per datasheet). The purely calculated worst case is thus just above the regulator's continuous current rating. In practice, full CM5 load, servo peak current, and maximum ToF activity never occur at exactly the same time; the measured total power of the complete system (7–10 W, see below) confirms a significantly lower real current demand. For future revisions, this is nevertheless noted as a point for improvement: a regulator with higher continuous current (e.g. 4 A) would create additional safety margin if further consumers are added.

<table width="100%" cellpadding="10" cellspacing="0" border="0"><tr><td bgcolor="#2E8B57" width="1%">&nbsp;</td><td bgcolor="#E2F3E5">
 <b>Result:</b> Worst-case peak current on the 5 V rail ≈ <b>3.2 A</b> versus a regulator capacity of <b>3 A</b> (AP3441SHE-7B) – however, the measured practical load of 7–10 W is significantly lower, since not all peaks occur simultaneously.
</td></tr></table>

### **Measured total power requirement**
The **measured total power requirement** of the system during operation is between about 7 W (low load) and 10 W (full computational load while driving).

### **Runtime calculation** 
- **Battery energy content:** 11.1 V × 0.55 Ah = 6.1 Wh<br>
- **Power consumption:** 7 to 10 watts <br>
- **Runtime (theoretical):** This results in a runtime of 36 to 52 minutes. <br>
- **Runtime (practical):** In test operation, the measured runtime to the shutdown threshold (3.5 V/cell) is usually about 40 minutes and thus matches the theoretical calculations well.

<table width="100%" cellpadding="10" cellspacing="0" border="0"><tr><td bgcolor="#2E8B57" width="1%">&nbsp;</td><td bgcolor="#E2F3E5">
 <b>Result:</b> The 3S LiPo (550 mAh) delivers a practical runtime of approx. <b>40 minutes</b> in test operation – this matches the theoretical calculation (36–52 min) and is sufficient for several competition runs per battery charge.
</td></tr></table>

### **Avoiding deep discharge**
To **avoid deep discharge**, the STM32 measures the battery voltage, switches off the motor at a cell voltage of 3.5 volts, and sends a signal to the Raspberry Pi, which then shuts down. It also cyclically moves the steering servo to indicate the empty battery.

### **Voltage supply of the individual components**
- **11.1 V direct**: N30 motor via the DRV8871 motor driver (H-bridge, 6.5–45 V, max. 3.6 A)
- **5 V via DC-DC converter:** Raspberry Pi CM5 via the 100-pin connectors on the self-developed baseboard; servo and all four VL53L8CX ToF sensors
- **3.3 V via linear regulator (AMS1117-3.3):** STM32F411, BNO086; the AMS1117's input supply comes from the 5 V rail via the GPIO header
- The Raspberry Pi Camera Module is powered exclusively via the **CM5's MIPI CSI interface**; no external wiring necessary

### **Failure modes in sensors and power supply**
To increase the reliability of our sensors and electronics, we have systematically summarized the main sources of error observed during development, along with their detection, effects, and countermeasures.

#### Table 12: Failure modes, detection, and countermeasures

<table align="center" border="1" style="border-collapse: collapse; border: 2px solid black;">

  <tr>
    <th bgcolor="#4A90C2" width="200" style="border: 1px solid black; border-bottom: 3px solid black; padding: 8px; color: white;">Failure</th>
    <th bgcolor="#4A90C2" width="260" style="border: 1px solid black; border-bottom: 3px solid black; padding: 8px; color: white;">Detection</th>
    <th bgcolor="#4A90C2" width="260" style="border: 1px solid black; border-bottom: 3px solid black; padding: 8px; color: white;">Effect</th>
    <th bgcolor="#4A90C2" width="260" style="border: 1px solid black; border-bottom: 3px solid black; padding: 8px; color: white;">Mitigation</th>
  </tr>

  <tr>
    <td bgcolor="#EAF4FB" style="border: 1px solid black; padding: 8px;">Gyro drift (residual error of the BNO086 accumulating over multiple laps)</td>
    <td bgcolor="#EAF4FB" style="border: 1px solid black; padding: 8px;">Deviation of the calculated heading from known target angles at turning points of the track</td>
    <td bgcolor="#EAF4FB" style="border: 1px solid black; padding: 8px;">Vehicle misses walls/corners, imprecise lane tracking</td>
    <td bgcolor="#EAF4FB" style="border: 1px solid black; padding: 8px;">Switch from BNO055 to the lower-drift <b>BNO086</b>; remaining residual error is compensated by a <b>rate calibration</b> before each run (cf. <a href="#table-10-summary-of-gyro-evaluation">Table 10</a>).</td>
  </tr>

  <tr>
    <td style="border: 1px solid black; padding: 8px;">ToF wall loss (sensor no longer detects a valid wall)</td>
    <td style="border: 1px solid black; padding: 8px;">Distance value is outside the plausibility range or timeout on the STM32</td>
    <td style="border: 1px solid black; padding: 8px;">Control logic receives no valid distance value and cannot safely execute the driving command</td>
    <td style="border: 1px solid black; padding: 8px;">Sensor height/mode optimized for maximum range (8×8/30 Hz, 130 cm); <b>last valid value is held until timeout</b></td>
  </tr>

  <tr>
    <td bgcolor="#EAF4FB" style="border: 1px solid black; padding: 8px;">Poor lighting (camera color detection disturbed by ambient light)</td>
    <td bgcolor="#EAF4FB" style="border: 1px solid black; padding: 8px;">Debug image before each run shows incomplete masks or an open flood-fill barrier at the black walls</td>
    <td bgcolor="#EAF4FB" style="border: 1px solid black; padding: 8px;">Obstacles/walls are detected incorrectly, route planning becomes faulty</td>
    <td bgcolor="#EAF4FB" style="border: 1px solid black; padding: 8px;"><b>Manual readjustment</b> of the V-maximum value and H/S/V limits before the competition (cf. <a href="#table-7-hsv-color-masks-and-calibration-parameters">Table 7</a>)</td>
  </tr>

  <tr>
    <td style="border: 1px solid black; padding: 8px;">Communication failure of small sensor boards
(unstable communication with more than two sensors)</td>
    <td style="border: 1px solid black; padding: 8px;">Missing/invalid sensor values and polling timeouts in tests with multiple sensors simultaneously</td>
    <td style="border: 1px solid black; padding: 8px;">Failure of the additional 45° sensors, resulting in a blind spot during diagonal wall approach</td>
    <td style="border: 1px solid black; padding: 8px;">Smaller sensor PCB design abandoned, reverted to the larger, stable boards. <b>The later full-scan strategy made the additional sensors unnecessary anyway.</b></td>
  </tr>

  <tr>
    <td bgcolor="#EAF4FB" style="border: 1px solid black; padding: 8px;">Undervoltage (battery voltage falls below shutdown threshold)</td>
    <td bgcolor="#EAF4FB" style="border: 1px solid black; padding: 8px;">STM32 continuously measures the battery cell voltage</td>
    <td bgcolor="#EAF4FB" style="border: 1px solid black; padding: 8px;">Motor/servo lose power, unreliable behavior up to a hard shutdown</td>
    <td bgcolor="#EAF4FB" style="border: 1px solid black; padding: 8px;"><b>Automatic shutdown at 3.5 V/cell</b>, signal to Raspberry Pi for an orderly shutdown, cyclic servo movement as a warning</td>
  </tr>

</table>
<br><br>

# **Software development**

## **Software architecture**
The software is split into **two separate processing layers**. 

The **high-level logic** runs on the Raspberry Pi Compute Module 5 (CM5): driving strategy, image processing, gyro evaluation, user interface, and logging. 

The **low-level control** resides on the STM32F411: motor control, encoder evaluation, servo control, and reading the four VL53L8CX time-of-flight sensors with a fixed cycle time.

This split has two advantages: the STM32 handles time-critical tasks without operating-system overhead. The CM5 can simultaneously perform computationally intensive tasks such as image processing and gyro fusion without blocking the sensor control loop. Communication between the two processors is via UART at 921,600 baud.

#### Figure 19: Overview of the system architecture

</div><div align="center">
    <a href="img/systemarchitektur_eng.png" target="_blank">
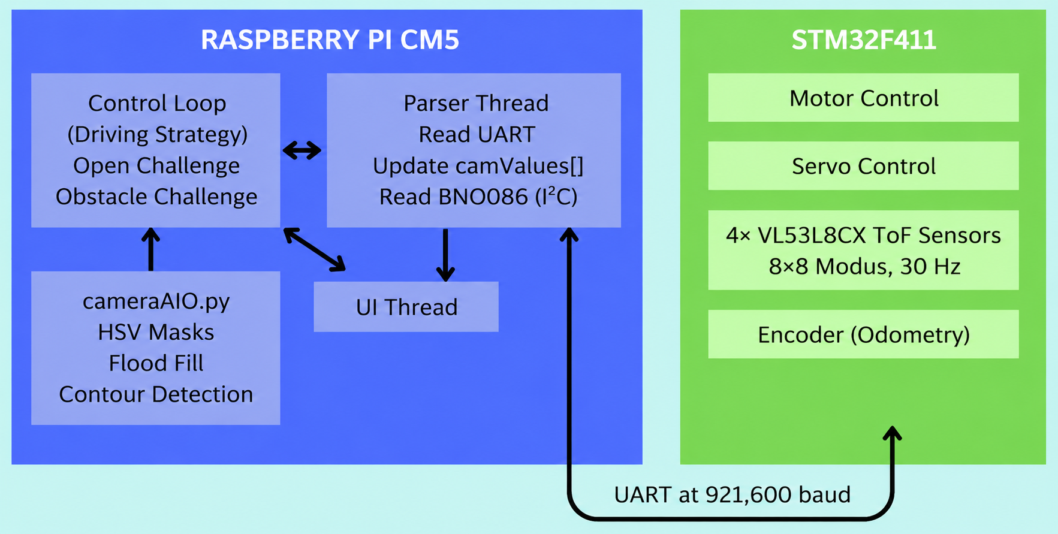
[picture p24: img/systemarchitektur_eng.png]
        
    </a>
</div>

#### Table 13: Task distribution of the software modules

<table align="center" border="1" style="border-collapse: collapse; border: 2px solid black;">

  <!-- Table header -->
  <tr>
    <th bgcolor="#4A90C2" width="240" style="border: 1px solid black; border-bottom: 3px solid black; padding: 8px; color: white;">Module / file</th>
    <th bgcolor="#4A90C2" width="180" style="border: 1px solid black; border-bottom: 3px solid black; padding: 8px; color: white;">Processor</th>
    <th bgcolor="#4A90C2" width="520" style="border: 1px solid black; border-bottom: 3px solid black; padding: 8px; color: white;">Main task</th>
  </tr>

  <!-- main.py -->
  <tr>
    <td bgcolor="#EAF4FB" style="border: 1px solid black; padding: 8px;"><code>main.py</code></td>
    <td bgcolor="#EAF4FB" style="border: 1px solid black; padding: 8px;">Raspberry Pi CM5</td>
    <td bgcolor="#EAF4FB" style="border: 1px solid black; padding: 8px;">System startup, start threads</td>
  </tr>

  <!-- parser.py -->
  <tr>
    <td style="border: 1px solid black; padding: 8px;"><code>parser.py</code></td>
    <td style="border: 1px solid black; padding: 8px;">Raspberry Pi CM5</td>
    <td style="border: 1px solid black; padding: 8px;">Serial communication with STM32, read BNO086 gyro</td>
  </tr>

  <!-- driveController.py -->
  <tr>
    <td bgcolor="#EAF4FB" style="border: 1px solid black; padding: 8px;"><code>driveController.py</code></td>
    <td bgcolor="#EAF4FB" style="border: 1px solid black; padding: 8px;">Raspberry Pi CM5</td>
    <td bgcolor="#EAF4FB" style="border: 1px solid black; padding: 8px;">Driving primitives: wall following, turns, distance driving, P-controller steering</td>
  </tr>

  <!-- openChallenge.py -->
  <tr>
    <td style="border: 1px solid black; padding: 8px;"><code>openChallenge.py</code></td>
    <td style="border: 1px solid black; padding: 8px;">Raspberry Pi CM5</td>
    <td style="border: 1px solid black; padding: 8px;">Opening challenge sequence control (3 laps)</td>
  </tr>

  <!-- obstacleChallenge.py -->
  <tr>
    <td bgcolor="#EAF4FB" style="border: 1px solid black; padding: 8px;"><code>obstacleChallenge.py</code>,<br><code>obstacleChallengeSingle.py</code></td>
    <td bgcolor="#EAF4FB" style="border: 1px solid black; padding: 8px;">Raspberry Pi CM5</td>
    <td bgcolor="#EAF4FB" style="border: 1px solid black; padding: 8px;">Scan phase, deterministic route, single- and two-obstacle handling per section</td>
  </tr>

  <!-- cameraAIO.py -->
  <tr>
    <td style="border: 1px solid black; padding: 8px;"><code>cameraAIO.py</code></td>
    <td style="border: 1px solid black; padding: 8px;">Raspberry Pi CM5</td>
    <td style="border: 1px solid black; padding: 8px;">Read camera image, HSV masks, flood fill, contour analysis</td>
  </tr>

  <!-- ui.py -->
  <tr>
    <td bgcolor="#EAF4FB" style="border: 1px solid black; padding: 8px;"><code>ui.py</code></td>
    <td bgcolor="#EAF4FB" style="border: 1px solid black; padding: 8px;">Raspberry Pi CM5</td>
    <td bgcolor="#EAF4FB" style="border: 1px solid black; padding: 8px;">Status display, user input</td>
  </tr>

  <!-- logger.py -->
  <tr>
    <td style="border: 1px solid black; padding: 8px;"><code>logger.py</code></td>
    <td style="border: 1px solid black; padding: 8px;">Raspberry Pi CM5</td>
    <td style="border: 1px solid black; padding: 8px;">Test logging</td>
  </tr>

  <!-- main.cpp -->
  <tr>
    <td bgcolor="#EAF4FB" style="border: 1px solid black; padding: 8px;"><code>main.cpp (STM32)</code></td>
    <td bgcolor="#EAF4FB" style="border: 1px solid black; padding: 8px;">STM32F411</td>
    <td bgcolor="#EAF4FB" style="border: 1px solid black; padding: 8px;">Motor PWM, encoder, servo, send ToF sensor data via JSON</td>
  </tr>

</table>

## **Threading and system flow**

Three functional layers run in parallel in the Raspberry Pi code:

- The **UI main thread** displays status data and reacts to keyboard input for starting and stopping. 
- The **parser thread** continuously reads the serial interface and updates the shared sensor values: distance fields of all four sensors, rotational speed, battery voltage, and heading. 
- The **control loop** executes the actual driving logic and writes target values for speed and steering angle back to the serial interface. 

## **Driving primitives in driveController.py**
<code>driveController.py</code> forms the abstraction layer between raw sensor values and the challenge scripts. It provides a **library of driving primitives** that internally combine heading control and acceleration ramps.

The **acceleration ramp** limits acceleration to 3 m/s² and braking deceleration to 8 m/s². This prevents the tires from spinning or locking up, which would distort the odometry values and the measured speed.

**Steering** uses two P-controllers: <code>pidSteer (Kp = 1.0)</code> for normal driving and <code>pidSteer2 (Kp = 0.5)</code> for smoother cornering with less overshoot.

Meaning of the Kp values: the controller calculates the steering angle offset (0–180°, center = 90°) directly from the heading error in degrees:

<table align="center" width="100%" cellpadding="8" cellspacing="0" border="0"><tr><td bgcolor="#B8D8EE" align="center">
steer = 90 − K<sub>p</sub> · error
</td></tr></table>

At Kp = 1.0, a 1° heading error corresponds exactly to a 1° steering correction; saturation (full lock) occurs at |error| ≥ 90°. At Kp = 0.5, it only occurs at |error| ≥ 180°, resulting in softer but more sluggish control behavior.

**Determining the values:** The Kp values were determined empirically. The starting point was Kp = 1.0, since the 1:1 mapping allows an intuitive initial estimate. When driving straight, the vehicle showed no oscillation – the mechanical inertia provides sufficient damping. During faster corner entry (turn()), however, Kp = 1.0 led to overshoot at the end of the turn. Halving it to Kp = 0.5 (pidSteer2) reduced the overshoot to below 3°.

**Why no I and D component:** An integral component is not necessary, since the gyro measures the absolute orientation and no permanent offset occurs. A D component would react to the measurement noise of the BNO086 and destabilize the steering.

**Wall-parallel distance keeping (side obedience):** When a primitive is called with an <code>avoidWall</code> parameter, <code>calcAccel()</code> additionally keeps the followed side wall within a target band of 150–350 mm using the corresponding side ToF sensor. If the car comes closer than 150 mm, an 8° steering bias away from the wall is applied; between 350 mm and 500 mm the bias points 8° toward the wall. A hysteresis (each correction is held for 250 mm of travel) prevents the steering from oscillating. This keeps the car parallel to the outer wall on the straights and provides the side obedience required in the obstacle challenge.

**Turn variants:** All three turning primitives first apply full steering lock and only hand over to the P-controller close to the target heading – <code>turn()</code> within 50°, <code>quickTurn()</code> within 20°. <code>tightTurn()</code> instead keeps full lock the whole time and tapers the speed (0.3 → 0.2 → 0.1 m/s) as the heading error shrinks, producing the tightest possible rotation for the scan positions and for parking.

The control is based on the following driving primitives: <br>

#### Table 14: Most important driving primitives and their function

<table align="center" border="1" style="border-collapse: collapse; border: 2px solid black;">

  <!-- Table header -->
  <tr>
    <th bgcolor="#4A90C2" width="230" style="border: 1px solid black; border-bottom: 3px solid black; padding: 8px; color: white;">Function</th>
    <th bgcolor="#4A90C2" width="280" style="border: 1px solid black; border-bottom: 3px solid black; padding: 8px; color: white;">Input</th>
    <th bgcolor="#4A90C2" width="500" style="border: 1px solid black; border-bottom: 3px solid black; padding: 8px; color: white;">Behavior</th>
  </tr>

  <!-- driveAlongWall -->
  <tr>
    <td bgcolor="#EAF4FB" style="border: 1px solid black; padding: 8px;"><code>driveAlongWall</code></td>
    <td bgcolor="#EAF4FB" style="border: 1px solid black; padding: 8px;">speed, heading, wall</td>
    <td bgcolor="#EAF4FB" style="border: 1px solid black; padding: 8px;">Drives until no wall is visible on the left or right</td>
  </tr>

  <!-- driveToWall -->
  <tr>
    <td style="border: 1px solid black; padding: 8px;"><code>driveToWall</code></td>
    <td style="border: 1px solid black; padding: 8px;">speed, heading, distance, wall</td>
    <td style="border: 1px solid black; padding: 8px;">Drives to target distance from the wall, ToF as stop criterion</td>
  </tr>

  <!-- driveAwayFromWall -->
  <tr>
    <td bgcolor="#EAF4FB" style="border: 1px solid black; padding: 8px;"><code>driveAwayFromWall</code></td>
    <td bgcolor="#EAF4FB" style="border: 1px solid black; padding: 8px;">speed, heading, distance, wall</td>
    <td bgcolor="#EAF4FB" style="border: 1px solid black; padding: 8px;">Moves away until minimum distance from the parameterized wall</td>
  </tr>

  <!-- driveDist -->
  <tr>
    <td style="border: 1px solid black; padding: 8px;"><code>driveDist</code></td>
    <td style="border: 1px solid black; padding: 8px;">speed, heading, distance [mm]</td>
    <td style="border: 1px solid black; padding: 8px;">Drives a fixed distance, encoder-based</td>
  </tr>

  <!-- turn -->
  <tr>
    <td bgcolor="#EAF4FB" style="border: 1px solid black; padding: 8px;"><code>turn</code></td>
    <td bgcolor="#EAF4FB" style="border: 1px solid black; padding: 8px;">speed, target heading</td>
    <td bgcolor="#EAF4FB" style="border: 1px solid black; padding: 8px;">Normal turn, stops when heading error &lt; threshold</td>
  </tr>

  <!-- quickTurn -->
  <tr>
    <td style="border: 1px solid black; padding: 8px;"><code>quickTurn</code></td>
    <td style="border: 1px solid black; padding: 8px;">speed, target heading</td>
    <td style="border: 1px solid black; padding: 8px;">Fast turn, maximum steering lock</td>
  </tr>

  <!-- tightTurn -->
  <tr>
    <td bgcolor="#EAF4FB" style="border: 1px solid black; padding: 8px;"><code>tightTurn</code></td>
    <td bgcolor="#EAF4FB" style="border: 1px solid black; padding: 8px;">speed, target heading</td>
    <td bgcolor="#EAF4FB" style="border: 1px solid black; padding: 8px;">Especially tight turn</td>
  </tr>

  <!-- brake -->
  <tr>
    <td style="border: 1px solid black; padding: 8px;"><code>brake</code></td>
    <td style="border: 1px solid black; padding: 8px; text-align: center;">–</td>
    <td style="border: 1px solid black; padding: 8px;">Target speed = 0, steering to 0°</td>
  </tr>

</table>

The specific **parameters** for the routines (e.g. the distance in the <code>driveToWall</code> function) were not calculated, but determined empirically through driving tests. Example: for <code>driveToWall</code>, the vehicle was driven with various threshold values and the value was adopted at which the following turn was initiated cleanly, without touching a wall.

## **Opening challenge driving strategy**
In the **opening challenge** (<code>openChallenge.py</code>), the car drives three complete laps. The car drives straight ahead until no wall is detected on the left or right, and remembers the driving direction based on this using the <code>findDirection</code> function. Each lap consists of four straights, each with a 90° turn:
- <code>driveAlongWall</code> – along the outer wall to the turn area
- <code>turn(−90°)</code> – initiate the turn via P-controller, target speed 1.8 m/s
- <code>driveDist(750 mm) + driveAlongWall</code> – next straight, target speed 2 m/s
- Repeat for all four sides of the course <br>

The pattern of straight and turn repeats four times per lap (one side of the course per iteration). After three complete laps (3 x 4 = 12 turns total), the vehicle stops with <code>driveAwayFromWall</code> in the middle of the starting zone. The target speed of 2 m/s on straights is a configured parameter value; the actual final speed depends on the acceleration ramp and the available track length.

#### Figure 20: Source code for the opening challenge

</div><div align="center">
    <a href="img/Code.png" target="_blank">
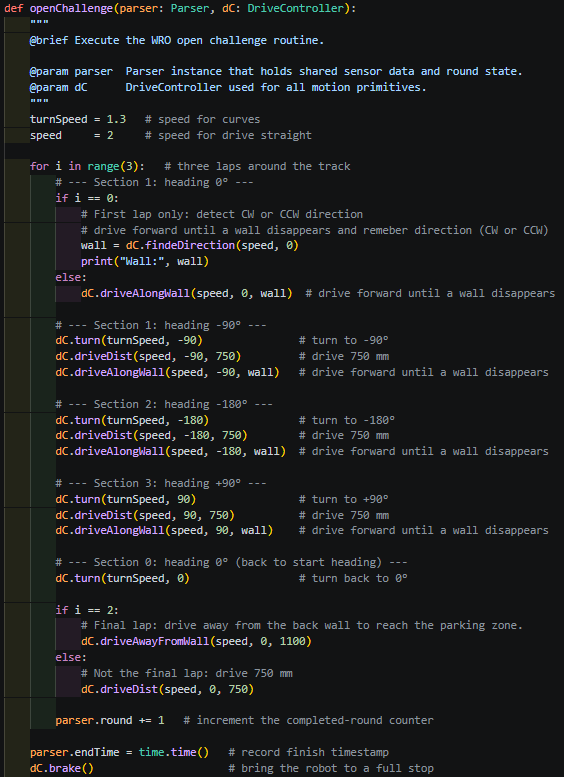
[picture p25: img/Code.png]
        
    </a>
</div>

## **Obstacle challenge driving strategy - strategy change**
### **Old strategy: scanning while driving**
The **original strategy** detected obstacles while driving. At the start of each straight, a photo was taken and the color of the first obstacle was determined. The system additionally scanned up to twice per section for further obstacles. This logic led to a state machine that was hard to maintain: up to three scan points per section, distance-dependent branches, and the camera in motion.

### **New strategy: full scan, fixed route**
The **new strategy fully separates detection and driving**. Right after program start, the car turns to 3 defined angles (<code>tightTurn</code>) and photographs the entire course. From these three photos, the colors of the obstacles across all four sections are detected at once and stored in <code>parser.obstacles[0..11]</code>. After that, the camera is no longer used – the route is deterministically fixed.  This version was the strategy we used for the **German national final in Trier**.

#### Figure 21: State diagram obstacle challenge – full-scan strategy

</div><div align="center">
    <a href="img/Zustandsdiagramm_Hindernisrennen_en.png" target="_blank">
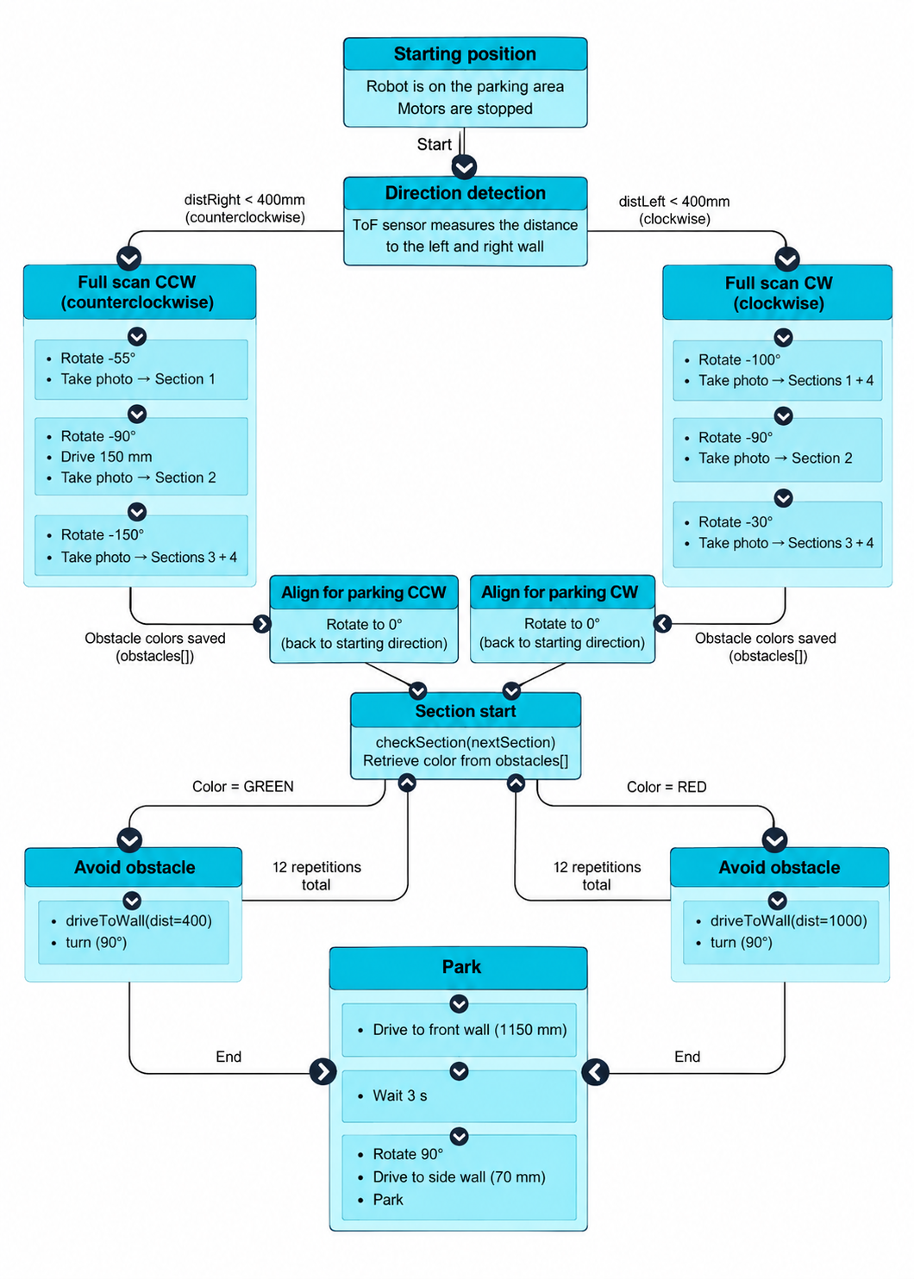
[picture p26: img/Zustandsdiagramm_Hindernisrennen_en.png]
        
    </a>
</div>

For the competition in Croatia, we developed the full-scan approach further: instead of physically turning the whole car to three different angles, the car now stays in a single fixed position and orientation, and only the **camera** is rotated – via the rotating camera tower described above (cf. [Further development: rotating camera tower](#further-development-rotating-camera-tower)). Using <code>parser.setTowerAngle()</code>, the tower is aimed at three different angles and a picture is taken at each of them. From these three images, all twelve obstacle slots <code>parser.obstacles[0..11]</code> are read by evaluating the direction-specific crop regions (<code>quaders</code>) defined in <code>cameraTower.py</code>. This eliminates the three separate turn-and-photograph maneuvers of the car entirely, making the scan faster and more repeatable, since the car no longer has to reach three different positions precisely before every run.

### **Passing two obstacles in one section**
The **German national rules limit each section to at most one obstacle**, so our original driving logic only ever had to react to a single obstacle color per section. The **international rules used in Croatia allow up to two obstacles in the same section**, which our old logic could not handle correctly: it evaluated only the first obstacle it detected and then drove straight to the next wall, ignoring a second obstacle that might require the car to switch sides. This is why the two-obstacle handling described below was implemented only when we started preparing for the competition in Croatia.

Each of the four course sections has three obstacle slots in <code>parser.obstacles[0..11]</code>, but the robot only ever has to react to **the obstacles actually present**. <code>parser.checkSectionMulti(section, mirror, colorMirror)</code> reads these slots and returns an ordered list of the colors found in that section, in the order in which the obstacles will be reached while driving. If a section contains only one obstacle, its color is duplicated in the list (<code>obstacleList[0] = obstacleList[1]</code>), so every section can be handled as if it always had exactly two entries — no special case is needed for sections with a single obstacle.

In <code>obstacleChallenge.py</code>, driving through a section is split into three steps:
- <code>FirstObstacle()</code> only looks at <code>sectionObstacleList[0]</code>. If the first obstacle is **green**, the robot turns left; if it is **red**, it first drives straight to the front wall before turning - identical to the original single-obstacle logic.
- If both list entries have the same color, <code>SameObstacles()</code> simply continues **driving straight** to the end of the section, using <code>driveToWall(..., avoidWall=dC.leftWall/dC.rightWall)</code> to avoid overshooting.
- If the two entries differ (red→green or green→red), <code>SecondObstacle()</code> drives only **half the distance** to the far wall (<code>driveDist(..., 300)</code>) before calling <code>wallDrive()</code>. This function steers the car 90° toward the wall on the **opposite** side, realigns its heading using the gyro (<code>dC.turn(0)</code>), and then continues driving straight to the end of the section.

<code>driveToWall(..., avoidWall=...)</code> continuously checks whether the inner wall is still present when the robot is driving on the left side of the section. If the wall is no longer detected, the robot has overshot the end of the section, so it briefly drives backwards.

To reuse the same functions for both driving directions, <code>checkSectionMulti</code> takes a <code>mirror</code> flag that swaps sections 1 and 3 and inverts the detected colors. This allows the same <code>FirstObstacle</code>/<code>SameObstacles</code>/<code>SecondObstacle</code> functions to work whether the robot drives clockwise or counter-clockwise.

### **Parking and un-parking**
The obstacle challenge starts and ends in the parking lot, so every run is framed by two dedicated maneuvers: **un-parking** at the start (<code>unParkCW</code>/<code>unParkCCW</code>) and **parking** at the end (<code>parkCW</code>/<code>parkCCW</code>). Because the parking lot is always positioned on the same side, mirroring the (un-)parking functions is not possible, so the two directions have separate implementations.

**Un-parking CW:** The un-parking maneuver is different based on if the first obstacle in the first section is red or green.
green:
1. turn to 40°
2. drive 200mm straight
3. turn back to 0°
4. drive to the end of the section <code>driveToWall()</code>
red:
1. turn to 90°
2. drive to inner wall <code>driveToWall()</code>
3. turn back to 0°
4. drive to the end of the section <code>driveToWall()</code>

**Un-parking CCW:** The un-parking maneuver is different based on if the first obstacle in the first section is red or green.
green:
1. turn to 90°
2. drive to inner wall <code>driveToWall()</code>
3. turn back to 0°
red:
1. turn to 40°
2. drive 350 mm straight (this drives between the right most obstacle and the outer parking lot wall)

**Parking:**
The parallel maneuver runs entirely at low speed (0.3–0.6 m/s) for precision and uses the ToF sensors on three sides for alignment:

1. Approach the front wall of the lot (<code>driveToWall</code>, front ToF) and straighten the heading (<code>tightTurn(0°)</code>).
2. Set the lateral position next to the lot from the side-wall ToF (<code>driveToWall</code> to 180 mm from the left/right wall), with an additional 300 mm offset if the previous section's last obstacle was green.
3. Swing the tail in with a forward–reverse–forward wiggle (<code>tightTurn(-45°)</code> forward, <code>tightTurn(-70°)</code> in reverse, <code>tightTurn(-90°)</code> forward).
4. Reverse into the lot until the rear ToF reports the back wall (<code>driveToWall</code> backward, back ToF) and finally straighten out (<code>tightTurn(0°)</code>).

## **Serial communication and data model**
**CM5** and **STM32** communicate via UART (/dev/ttyAMA0, 921,600 baud). Per transmission cycle, the STM32 sends a complete status packet to the CM5; the CM5 responds with a control packet. The parser thread on the CM5 processes incoming packets asynchronously and writes the values into shared fields of the parser object.
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

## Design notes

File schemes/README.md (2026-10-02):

# Electromechanical diagrams

This directory contains a schematic diagram of the electromechanical components illustrating all the elements (electronic components and motors) used in the vehicle and how they connect to each other.

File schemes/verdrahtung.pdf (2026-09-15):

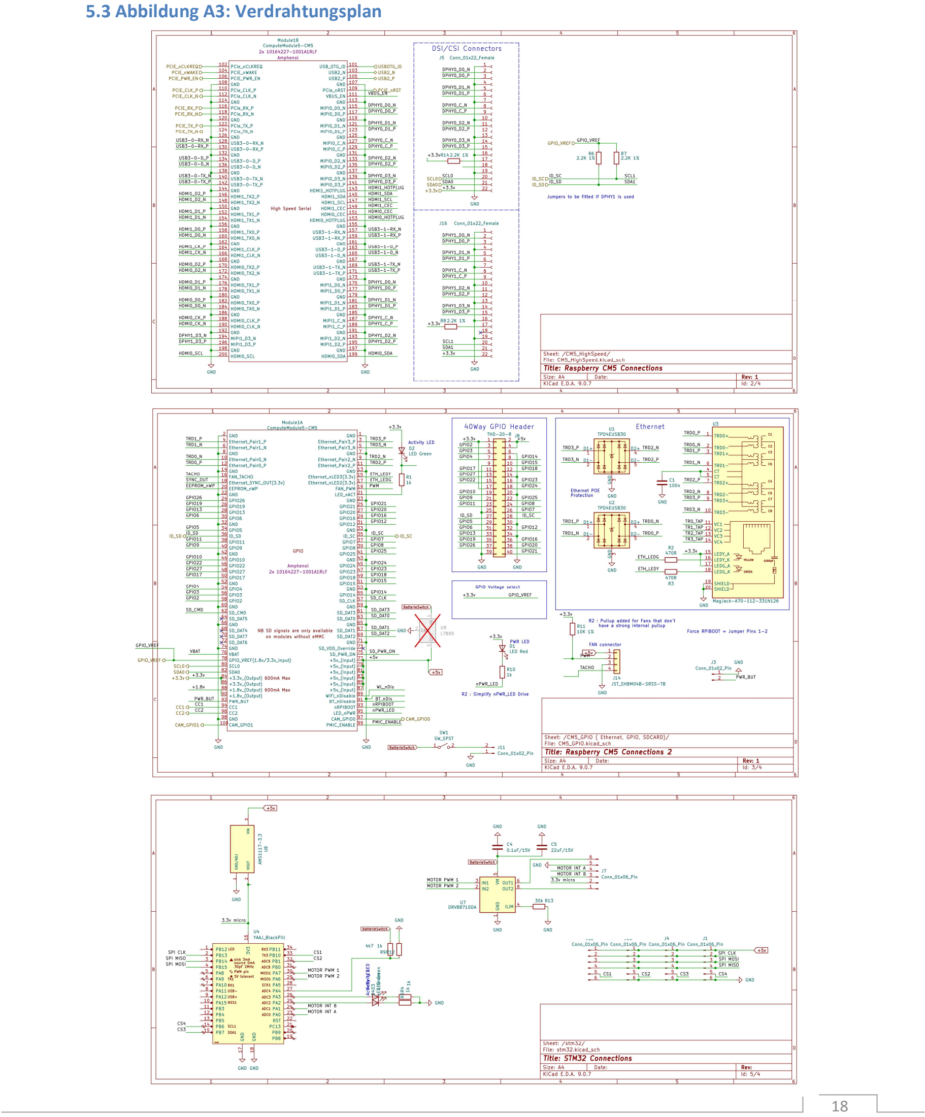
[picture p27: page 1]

18

### 5.3 Abbildung A3: Verdrahtungsplan

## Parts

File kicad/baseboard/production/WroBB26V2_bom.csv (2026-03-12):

Designator | Footprint | Quantity | Value | LCSC Part #
C1, C18, C9 | 0603 | 3 | 100n | C14663
C4 | 0603 | 1 | 0.1uF/15V | C14663
C5 | 0805 | 1 | 22uF/15V | C45783
D1 | 0805 | 1 | LED Red | C84256
D2 | 0805 | 1 | LED Green | C2297
D3 | 0805 | 1 | LED Green
D4 | 0805 | 1 | LED Green | C2296
J1, J10, J12, J4, J7 | JST_XH_B6B-XH-A_1x06_P2.50mm_Vertical | 5 | Conn_01x06_Pin | C160255
J11, J3 | JST_EH_B2B-EH-A_1x02_P2.50mm_Vertical | 2 | Conn_01x02_Pin
J14 | JST_SH_BM04B-SRSS-TB_1x04-1MP_P1.00mm_Vertical | 1 | JST_SHBM04B-SRSS-TB | C160390
J15 | JST_XH_B3B-XH-A_1x03_P2.50mm_Vertical | 1 | Conn_01x03_Pin
J16, J5 | AMPHENOL_F305-1A7H1-21022-E100 | 2 | Conn_01x22_Female | C3168287
J17 | DfRobot BNO055 | 1 | DfRobot BNO055
J18 | JST_XH_B5B-XH-AM_1x05_P2.50mm_Vertical | 1 | Conn_01x05
J2, J6 | AMPHENOL_10164227-1001A1RLF | 2 | 10164227-1001A1RLF | C7435219
J8 | PinHeader_2x20_P2.54mm_Vertical | 1 | THD-20-R
MODULE1 | Raspberry-Pi-5-Compute-Module | 1 | ComputeModule5-CM5
R1, R10, R12, R4, R5 | 0603 | 5 | 1k | C21190
R11 | 0603 | 1 | 10K 1% | C25804
R13 | 0603 | 1 | 30k | C22984
R14 | 0603 | 1 | 2.2K 1% | LCSC Part #
R2, R3 | 0603 | 2 | 470R | C23179
R6, R7, R8 | 0603 | 3 | 2.2K 1% | C4190
R9 | 0603 | 1 | 4k7 | C23162
SW1 | SW_DIP_SPSTx01_Slide_9.78x4.72mm_W7.62mm_P2.54mm | 1 | SW_SPST
U1, U2 | USON-10_2.5x1.0mm_P0.5mm | 2 | TPD4EUSB30 | C90627
U3 | TRJG0926HENL | 1 | MagJack-A70-112-331N126 | C22457393
U6 | DIP-40_W15.24mm_Socket | 1 | STM32F411_BlackPill
U7 | Texas_HTSOP-8-1EP_3.9x4.9mm_P1.27mm_EP2.95x4.9mm_Mask2.4x3.1mm_ThermalVias | 1 | DRV8871DDA | C75864
U8 | SOT-223-3_TabPin2 | 1 | AMS1117-3.3 | C6186

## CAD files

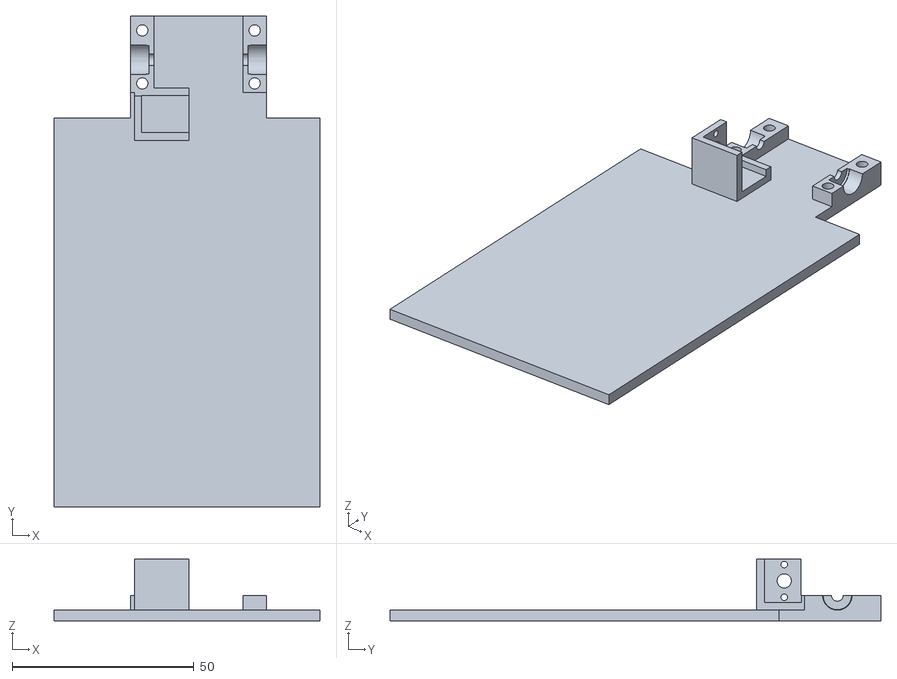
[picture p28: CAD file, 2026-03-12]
models/Lowderdeck.stl
73.0 x 135.0 x 17.0

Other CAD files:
cad/Front Wheel.f3d
cad/Steering knuckle2.f3d
cad/base and middle plate.f3z
cad/radmutter.f3d
cad/support bridge.f3d
cad/top plate.f3z
cad/track_rod.f3d
cad/wheel placeholder (optional).f3d

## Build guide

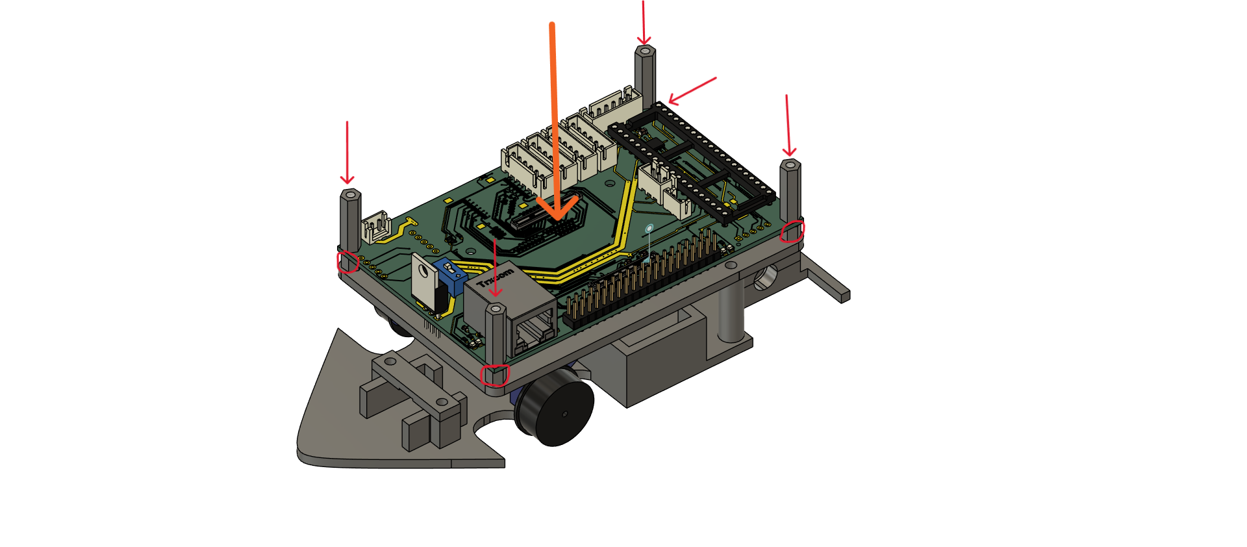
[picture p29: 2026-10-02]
img/construction/middle deck assembly 3.png

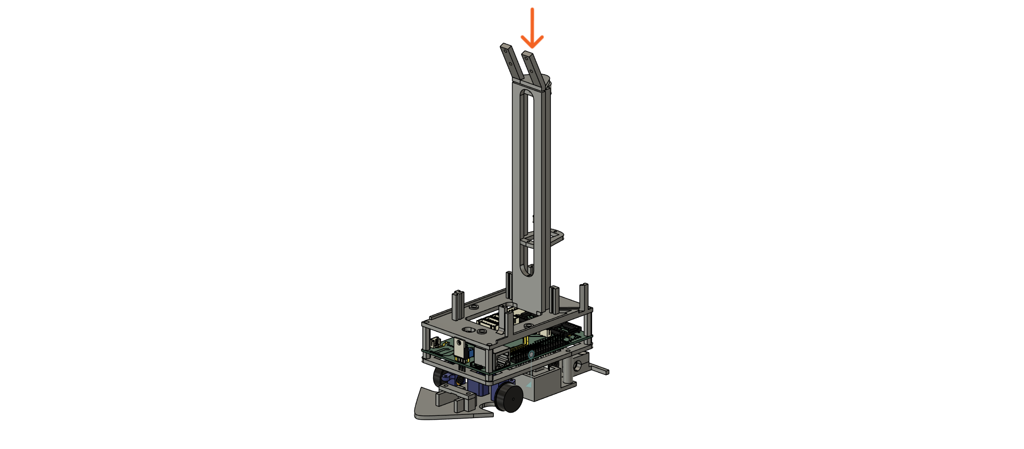
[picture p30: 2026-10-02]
img/construction/top deck assembly 2.png

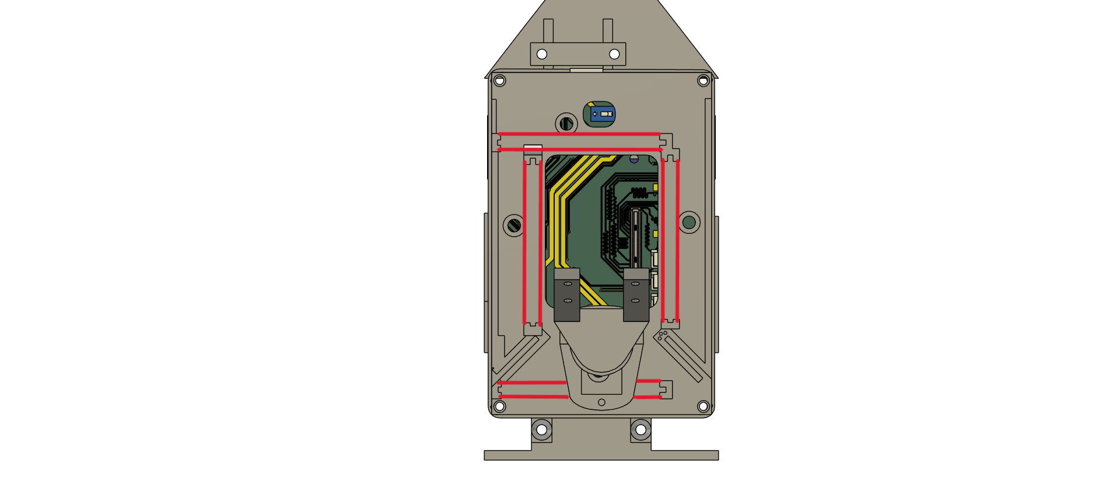
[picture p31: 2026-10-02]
img/construction/top deck assembly 1b.png

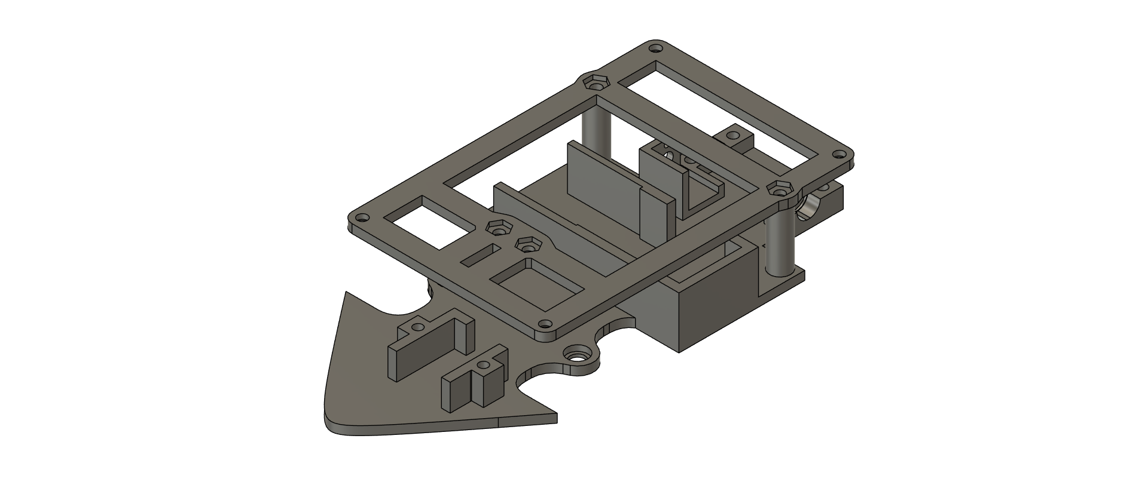
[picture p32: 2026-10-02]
img/construction/Bodenplatte richtige version.png

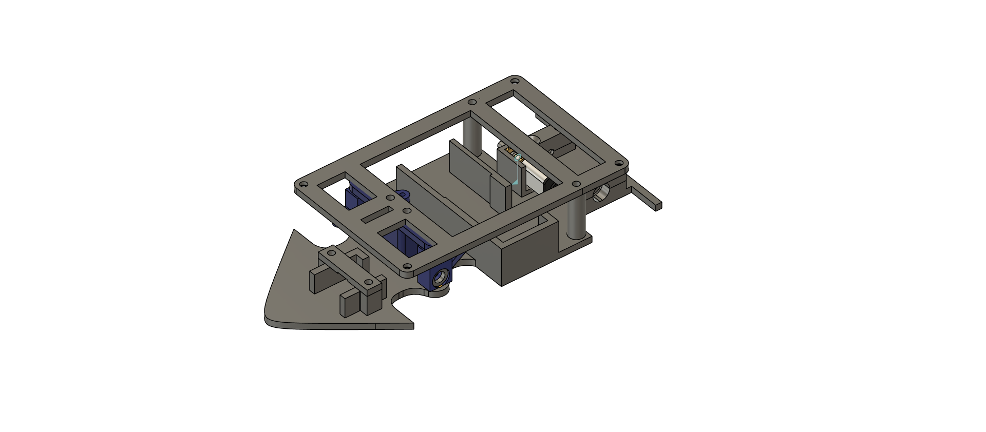
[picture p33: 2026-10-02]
img/construction/middle deck assembly 1.png

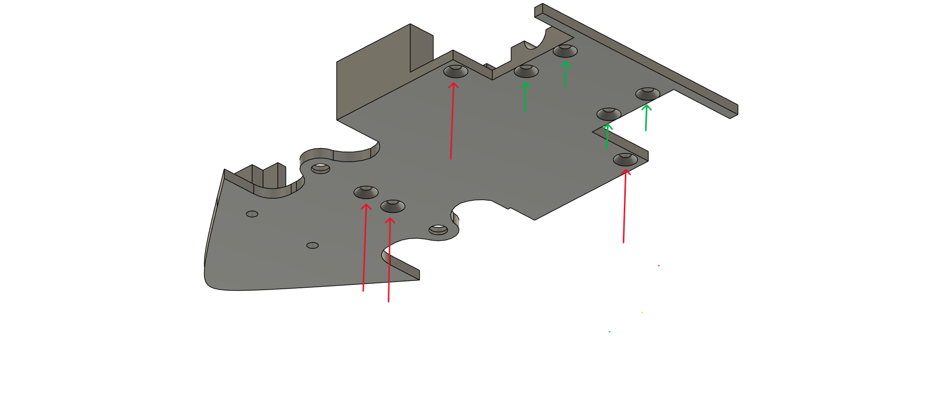
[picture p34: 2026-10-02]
img/construction/Bodenplatte.png

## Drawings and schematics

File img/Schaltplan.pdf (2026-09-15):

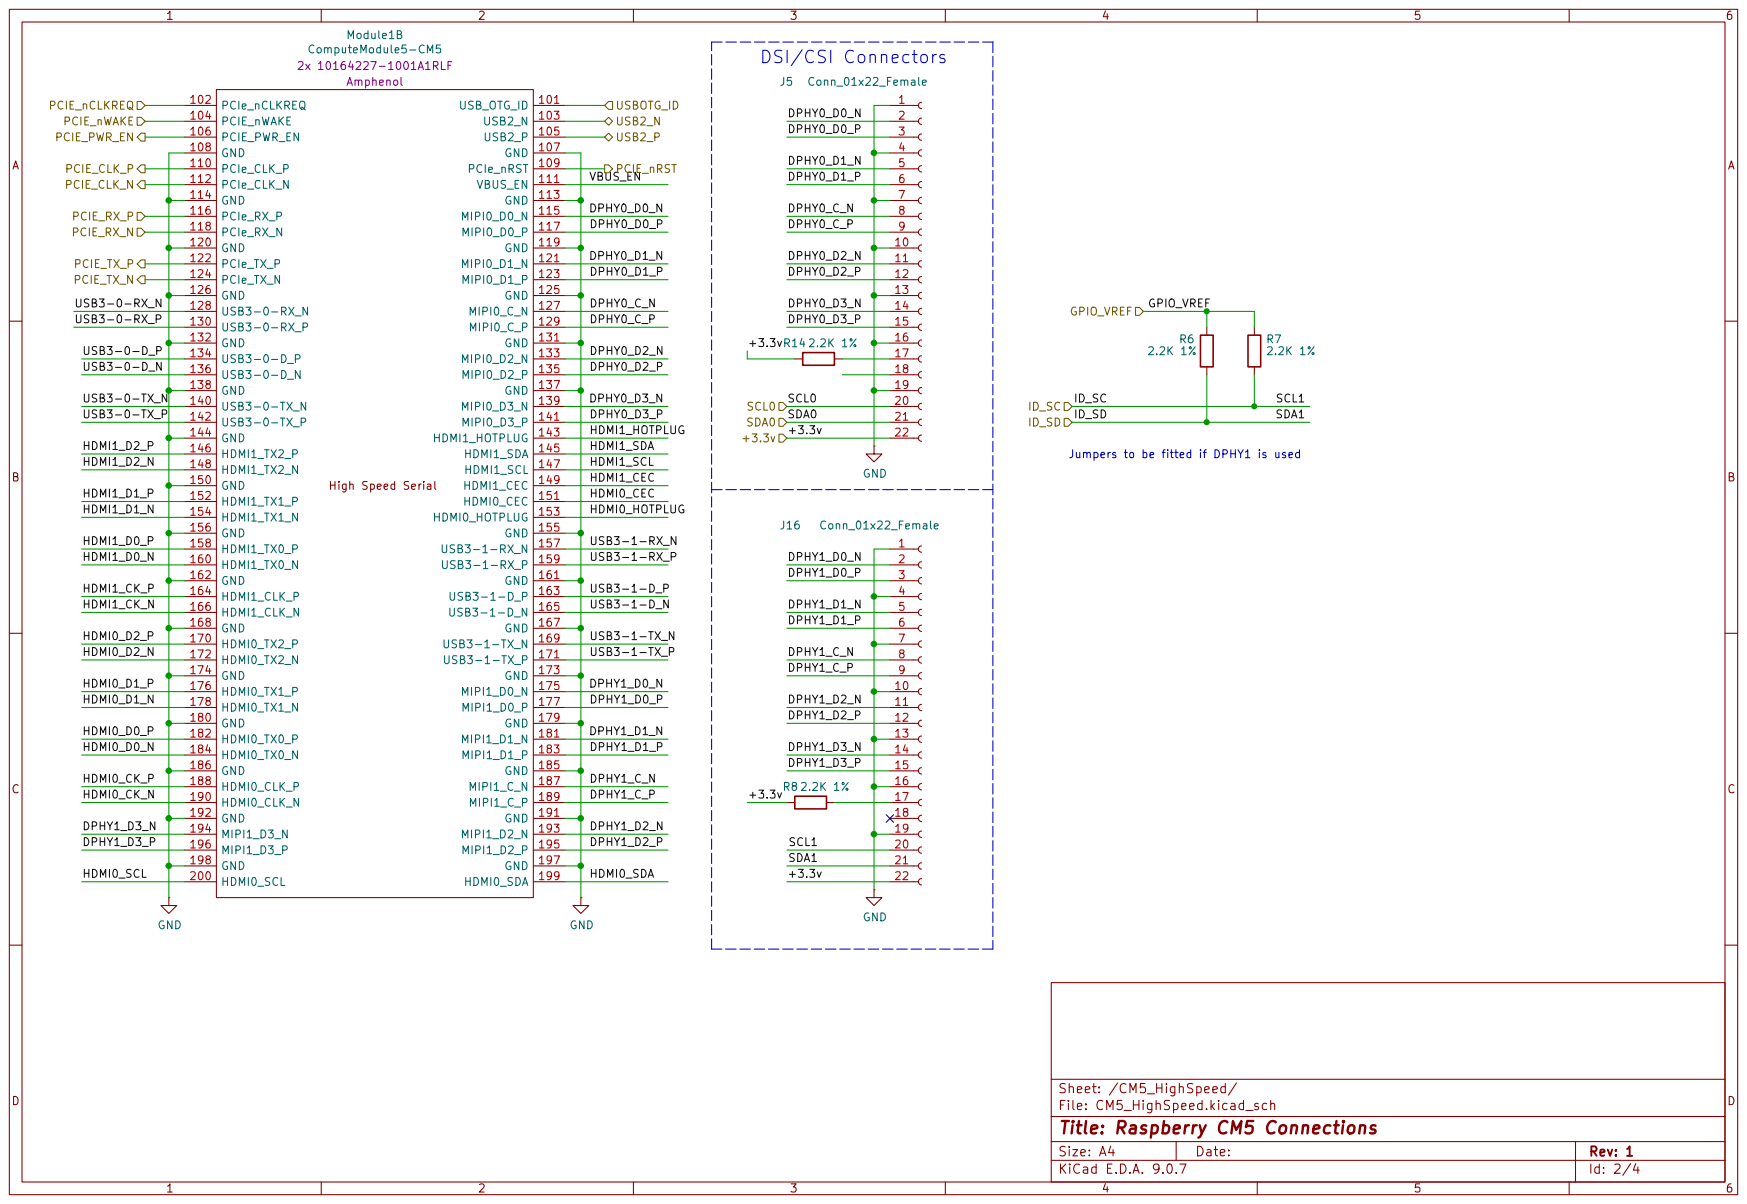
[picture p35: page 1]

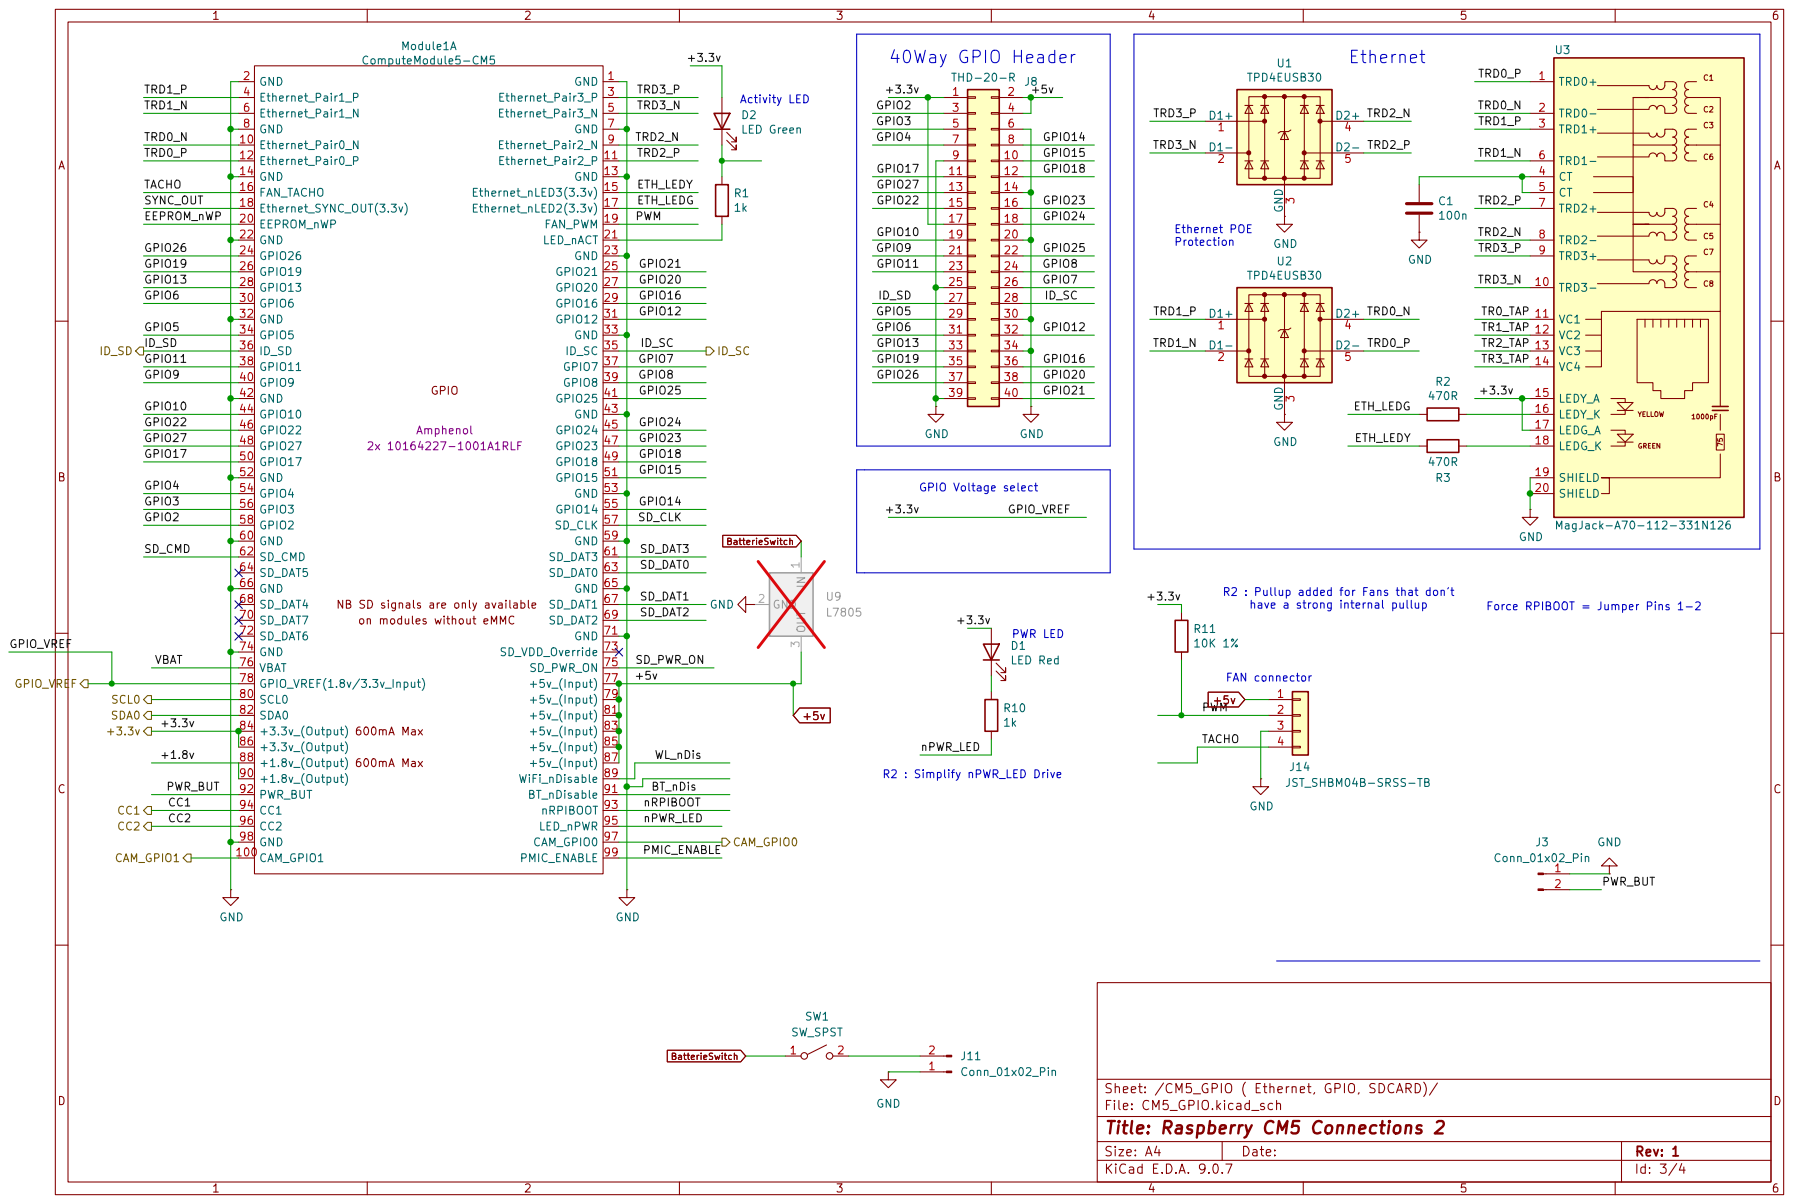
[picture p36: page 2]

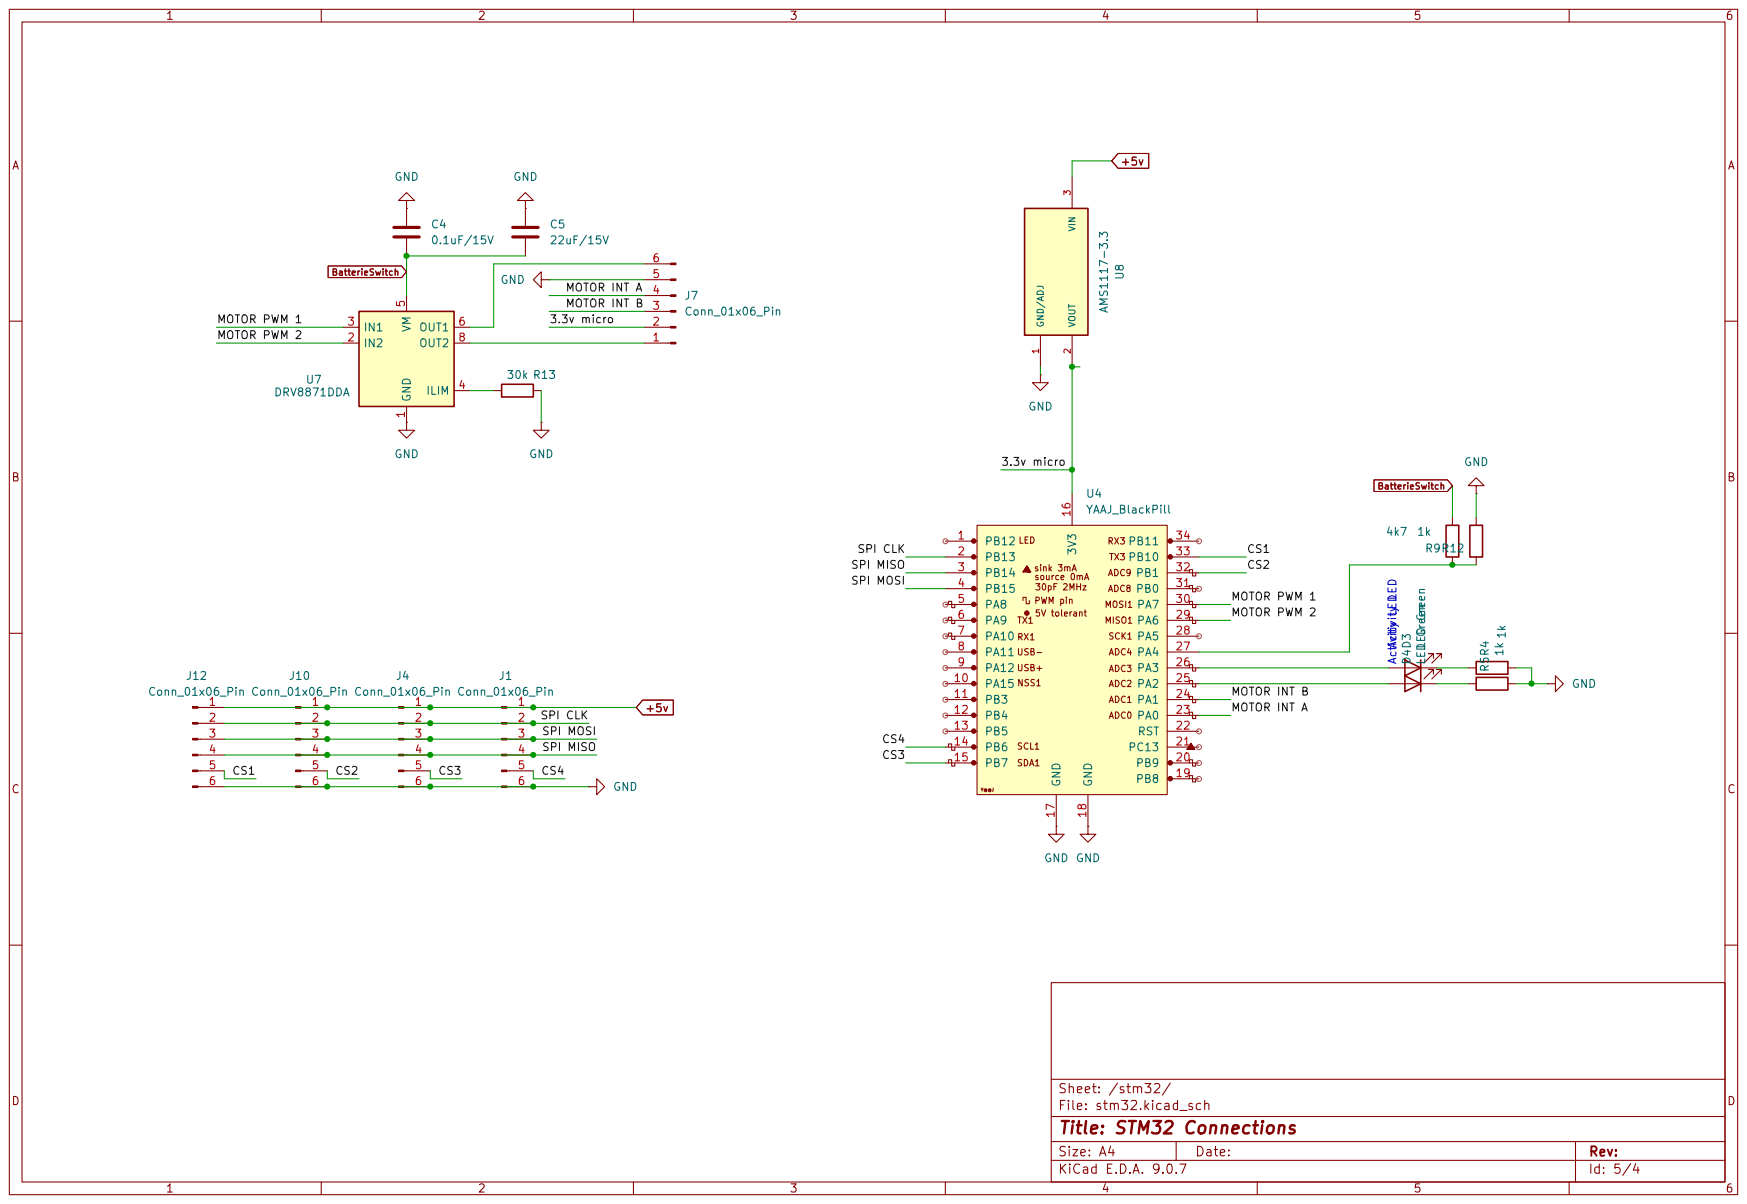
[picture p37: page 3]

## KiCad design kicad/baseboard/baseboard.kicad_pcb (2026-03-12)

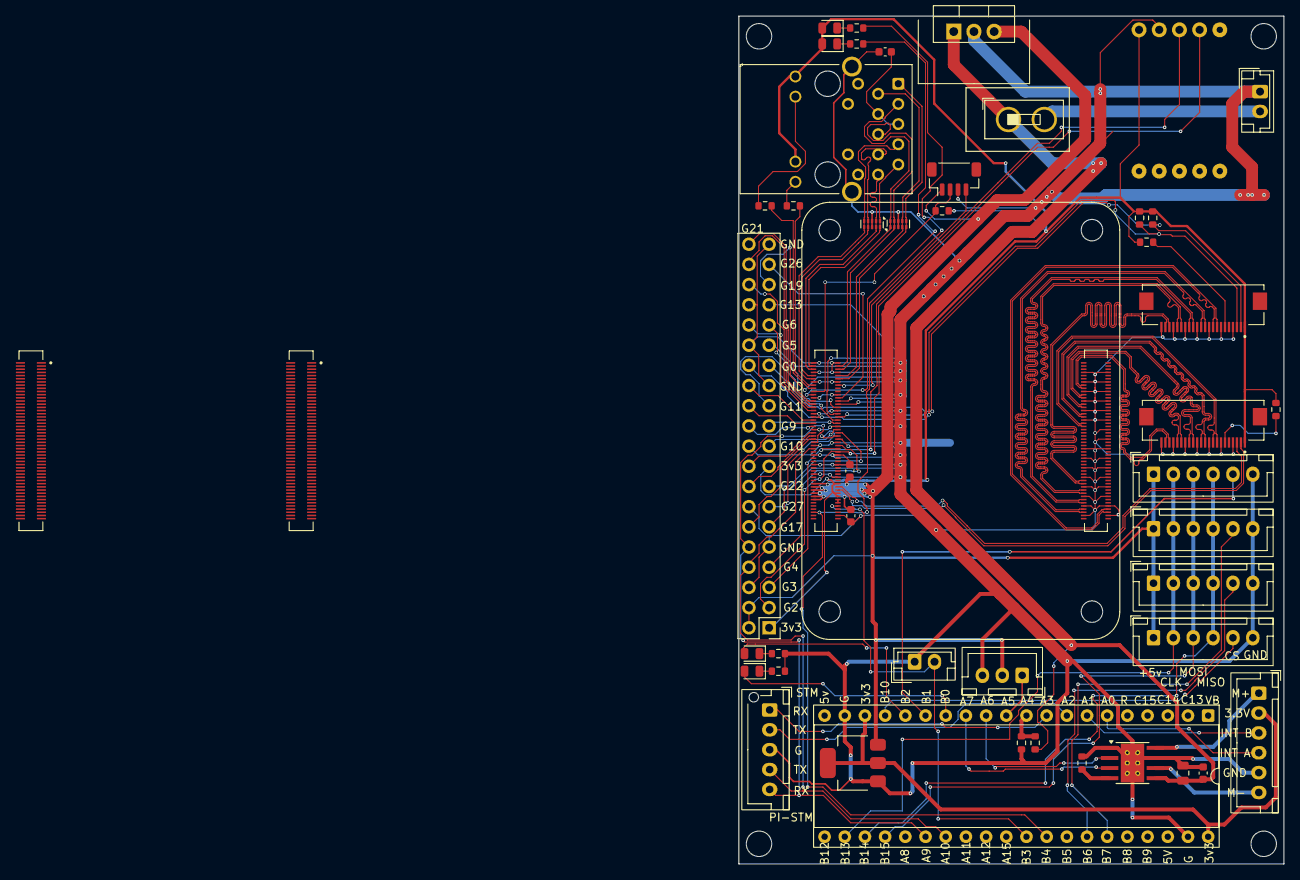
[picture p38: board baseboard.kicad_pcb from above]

Board: 2 copper layers, 68.6 x 106.7 mm, 52 parts (0 on the bottom side), 101 nets.

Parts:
C1, C9, C18: 100n; C_0603_1608Metric
C4: 0.1uF/15V; C_0603_1608Metric
C5: 22uF/15V; C_0805_2012Metric
D1: LED Red; LED_0805_2012Metric
D2, D3, D4: LED Green; LED_0805_2012Metric
H1, H2, H3, H4: MountingHole; MountingHole_3.2mm_M3_DIN965
J1, J4, J7, J10, J12: Conn_01x06_Pin; JST_XH_B6B-XH-A_1x06_P2.50mm_Vertical
J2, J6: 10164227-1001A1RLF; AMPHENOL_10164227-1001A1RLF
J3, J11: Conn_01x02_Pin; JST_EH_B2B-EH-A_1x02_P2.50mm_Vertical
J5, J16: Conn_01x22_Female; AMPHENOL_F305-1A7H1-21022-E100
J8: THD-20-R; PinHeader_2x20_P2.54mm_Vertical
J14: JST_SHBM04B-SRSS-TB; JST_SH_BM04B-SRSS-TB_1x04-1MP_P1.00mm_Vertical
J15: Conn_01x03_Pin; JST_XH_B3B-XH-A_1x03_P2.50mm_Vertical
J17: DfRobot BNO055
J18: Conn_01x05; JST_XH_B5B-XH-AM_1x05_P2.50mm_Vertical
Module1: ComputeModule5-CM5; Raspberry-Pi-5-Compute-Module
R1, R4, R5, R10, R12: 1k; R_0603_1608Metric
R2, R3: 470R; R_0603_1608Metric
R6, R7, R8, R14: 2.2K 1%; R_0603_1608Metric
R9: 4k7; R_0603_1608Metric
R11: 10K 1%; R_0603_1608Metric
R13: 30k; R_0603_1608Metric
SW1: SW_SPST; SW_DIP_SPSTx01_Slide_9.78x4.72mm_W7.62mm_P2.54mm
U1, U2: TPD4EUSB30; USON-10_2.5x1.0mm_P0.5mm
U3: MagJack-A70-112-331N126; TRJG0926HENL
U6: STM32F411_BlackPill; DIP-40_W15.24mm_Socket
U7: DRV8871DDA; Texas_HTSOP-8-1EP_3.9x4.9mm_P1.27mm_EP2.95x4.9mm_Mask2.4x3.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
U8: AMS1117-3.3; SOT-223-3_TabPin2
U9: L7805; TO-220-3_Vertical

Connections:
+5v: C9.1, C18.1, J1.1, J4.1, J8.2, J8.4, J10.1, J12.1, J14.1, J15.2, Module1.77 (+5v_(Input)), Module1.79 (+5v_(Input)), Module1.81 (+5v_(Input)), Module1.83 (+5v_(Input)), Module1.85 (+5v_(Input)), Module1.87 (+5v_(Input)), U8.3 (VIN), U9.3 (OUT)
/+3.3v: D1.2 (A), D2.2 (A), J5.1, J8.1, J8.17, J16.1, J17.1 (VCC_33), Module1.78 (GPIO_VREF(1.8v/3.3v_Input)), Module1.84 (+3.3v_(Output)), Module1.86 (+3.3v_(Output)), R6.1, R7.1, R8.1, R11.1, R14.1, U3.15 (LEDY_A), U3.17 (LEDG_A)
/CM5_GPIO ( Ethernet, GPIO, SDCARD)/+1.8v: Module1.88 (+1.8v_(Output)), Module1.90 (+1.8v_(Output))
/CM5_GPIO ( Ethernet, GPIO, SDCARD)/ETH_LEDG: Module1.17 (Ethernet_nLED2(3.3v)), R2.2
/CM5_GPIO ( Ethernet, GPIO, SDCARD)/ETH_LEDY: Module1.15 (Ethernet_nLED3(3.3v)), R3.2
/CM5_GPIO ( Ethernet, GPIO, SDCARD)/GPIO2: J8.3, J17.4 (SDA), Module1.58 (GPIO2)
/CM5_GPIO ( Ethernet, GPIO, SDCARD)/GPIO3: J8.5, J17.3 (SCL), Module1.56 (GPIO3)
/CM5_GPIO ( Ethernet, GPIO, SDCARD)/GPIO4: J8.7, Module1.54 (GPIO4)
/CM5_GPIO ( Ethernet, GPIO, SDCARD)/GPIO5: J8.29, Module1.34 (GPIO5)
/CM5_GPIO ( Ethernet, GPIO, SDCARD)/GPIO6: J8.31, Module1.30 (GPIO6)
/CM5_GPIO ( Ethernet, GPIO, SDCARD)/GPIO7: J8.26, Module1.37 (GPIO7)
/CM5_GPIO ( Ethernet, GPIO, SDCARD)/GPIO8: J8.24, Module1.39 (GPIO8)
/CM5_GPIO ( Ethernet, GPIO, SDCARD)/GPIO9: J8.21, Module1.40 (GPIO9)
/CM5_GPIO ( Ethernet, GPIO, SDCARD)/GPIO10: J8.19, Module1.44 (GPIO10)
/CM5_GPIO ( Ethernet, GPIO, SDCARD)/GPIO11: J8.23, Module1.38 (GPIO11)
/CM5_GPIO ( Ethernet, GPIO, SDCARD)/GPIO12: J8.32, Module1.31 (GPIO12)
/CM5_GPIO ( Ethernet, GPIO, SDCARD)/GPIO13: J8.33, Module1.28 (GPIO13)
/CM5_GPIO ( Ethernet, GPIO, SDCARD)/GPIO16: J8.36, Module1.29 (GPIO16)
/CM5_GPIO ( Ethernet, GPIO, SDCARD)/GPIO17: J8.11, Module1.50 (GPIO17)
/CM5_GPIO ( Ethernet, GPIO, SDCARD)/GPIO18: J8.12, Module1.49 (GPIO18)
/CM5_GPIO ( Ethernet, GPIO, SDCARD)/GPIO19: J8.35, Module1.26 (GPIO19)
/CM5_GPIO ( Ethernet, GPIO, SDCARD)/GPIO20: J8.38, Module1.27 (GPIO20)
/CM5_GPIO ( Ethernet, GPIO, SDCARD)/GPIO21: J8.40, Module1.25 (GPIO21)
/CM5_GPIO ( Ethernet, GPIO, SDCARD)/GPIO22: J8.15, Module1.46 (GPIO22)
/CM5_GPIO ( Ethernet, GPIO, SDCARD)/GPIO23: J8.16, Module1.47 (GPIO23)
/CM5_GPIO ( Ethernet, GPIO, SDCARD)/GPIO24: J8.18, Module1.45 (GPIO24)
/CM5_GPIO ( Ethernet, GPIO, SDCARD)/GPIO25: J8.22, Module1.41 (GPIO25)
/CM5_GPIO ( Ethernet, GPIO, SDCARD)/GPIO26: J8.37, Module1.24 (GPIO26)
/CM5_GPIO ( Ethernet, GPIO, SDCARD)/GPIO27: J8.13, Module1.48 (GPIO27)
/CM5_GPIO ( Ethernet, GPIO, SDCARD)/ID_SC: J8.28, J16.3, Module1.35 (ID_SC), R7.2
/CM5_GPIO ( Ethernet, GPIO, SDCARD)/ID_SD: J8.27, J16.2, Module1.36 (ID_SD), R6.2
/CM5_GPIO ( Ethernet, GPIO, SDCARD)/PWM: J14.2, Module1.19 (FAN_PWM), R11.2
/CM5_GPIO ( Ethernet, GPIO, SDCARD)/TACHO: J14.4, Module1.16 (FAN_TACHO)
/CM5_GPIO ( Ethernet, GPIO, SDCARD)/TRD0_N: Module1.10 (Ethernet_Pair0_N), U2.4 (D2+), U2.7, U3.2 (TRD0-)
/CM5_GPIO ( Ethernet, GPIO, SDCARD)/TRD0_P: Module1.12 (Ethernet_Pair0_P), U2.5 (D2-), U2.6, U3.1 (TRD0+)
/CM5_GPIO ( Ethernet, GPIO, SDCARD)/TRD1_N: Module1.6 (Ethernet_Pair1_N), U2.2 (D1-), U2.9, U3.6 (TRD1-)
/CM5_GPIO ( Ethernet, GPIO, SDCARD)/TRD1_P: Module1.4 (Ethernet_Pair1_P), U2.1 (D1+), U2.10, U3.3 (TRD1+)
/CM5_GPIO ( Ethernet, GPIO, SDCARD)/TRD2_N: Module1.9 (Ethernet_Pair2_N), U1.4 (D2+), U1.7, U3.8 (TRD2-)
/CM5_GPIO ( Ethernet, GPIO, SDCARD)/TRD2_P: Module1.11 (Ethernet_Pair2_P), U1.5 (D2-), U1.6, U3.7 (TRD2+)
/CM5_GPIO ( Ethernet, GPIO, SDCARD)/TRD3_N: Module1.5 (Ethernet_Pair3_N), U1.2 (D1-), U1.9, U3.10 (TRD3-)
/CM5_GPIO ( Ethernet, GPIO, SDCARD)/TRD3_P: Module1.3 (Ethernet_Pair3_P), U1.1 (D1+), U1.10, U3.9 (TRD3+)
/CM5_HighSpeed/DPHY0_C_N: J5.15, Module1.127 (MIPI0_C_N)
/CM5_HighSpeed/DPHY0_C_P: J5.14, Module1.129 (MIPI0_C_P)
/CM5_HighSpeed/DPHY0_D0_N: J5.21, Module1.115 (MIPI0_D0_N)
/CM5_HighSpeed/DPHY0_D0_P: J5.20, Module1.117 (MIPI0_D0_P)
/CM5_HighSpeed/DPHY0_D1_N: J5.18, Module1.121 (MIPI0_D1_N)
/CM5_HighSpeed/DPHY0_D1_P: J5.17, Module1.123 (MIPI0_D1_P)
/CM5_HighSpeed/DPHY0_D2_N: J5.12, Module1.133 (MIPI0_D2_N)
/CM5_HighSpeed/DPHY0_D2_P: J5.11, Module1.135 (MIPI0_D2_P)
/CM5_HighSpeed/DPHY0_D3_N: J5.9, Module1.139 (MIPI0_D3_N)
/CM5_HighSpeed/DPHY0_D3_P: J5.8, Module1.141 (MIPI0_D3_P)
/CM5_HighSpeed/DPHY1_C_N: J16.15, Module1.187 (MIPI1_C_N)
/CM5_HighSpeed/DPHY1_C_P: J16.14, Module1.189 (MIPI1_C_P)
/CM5_HighSpeed/DPHY1_D0_N: J16.21, Module1.175 (MIPI1_D0_N)
/CM5_HighSpeed/DPHY1_D0_P: J16.20, Module1.177 (MIPI1_D0_P)
/CM5_HighSpeed/DPHY1_D1_N: J16.18, Module1.181 (MIPI1_D1_N)
/CM5_HighSpeed/DPHY1_D1_P: J16.17, Module1.183 (MIPI1_D1_P)
/CM5_HighSpeed/DPHY1_D2_N: J16.12, Module1.193 (MIPI1_D2_N)
/CM5_HighSpeed/DPHY1_D2_P: J16.11, Module1.195 (MIPI1_D2_P)
/CM5_HighSpeed/DPHY1_D3_N: J16.9, Module1.194 (MIPI1_D3_N)
/CM5_HighSpeed/DPHY1_D3_P: J16.8, Module1.196 (MIPI1_D3_P)
/CM5_HighSpeed/SCL0: J5.3, Module1.80 (SCL0)
/CM5_HighSpeed/SDA0: J5.2, Module1.82 (SDA0)
/stm32/3.3v micro: J7.2, U6.18 (3.3V), U6.40 (3,3V), U8.2 (VOUT)
/stm32/CS1: J12.5, U6.17 (PB10)
/stm32/CS2: J10.5, U6.15 (PB1)
/stm32/CS3: J4.5, U6.35 (B7)
/stm32/CS4: J1.5, U6.34 (B6)
/stm32/MOTOR INT A: J7.4, U6.6 (PA0)
/stm32/MOTOR INT B: J7.3, U6.7 (PA1)
/stm32/MOTOR PWM 1: U6.13 (PA7), U7.3 (IN1)
/stm32/MOTOR PWM 2: U6.12 (PA6), U7.2 (IN2)
/stm32/SPI CLK: J1.2, J4.2, J10.2, J12.2, U6.22 (B13)
/stm32/SPI MISO: J1.4, J4.4, J10.4, J12.4, U6.23 (B14)
/stm32/SPI MOSI: J1.3, J4.3, J10.3, J12.3, U6.24 (B15)
BatterieSwitch: C4.2, C5.2, R9.2, SW1.1 (A), U7.5 (VM), U9.1 (IN)
GND: C1.2, C4.1, C5.1, C9.2, C18.2, J1.6, J3.1, J4.6, J5.4, J5.7, J5.10, J5.13, J5.16, J5.19, J5.22, J7.5, J8.6, J8.9, J8.14, J8.20, J8.25, J8.30, J8.34, J8.39, J10.6, J11.1, J12.6, J14.3, J15.3, J16.4, J16.7, J16.10, J16.13, J16.16, J16.19, J16.22, J17.2 (GND), J18.3, Module1.1 (GND), Module1.2 (GND), Module1.7 (GND), Module1.8 (GND), Module1.13 (GND), Module1.14 (GND), Module1.22 (GND), Module1.23 (GND), Module1.32 (GND), Module1.33 (GND), Module1.42 (GND), Module1.43 (GND), Module1.52 (GND), Module1.53 (GND), Module1.59 (GND), Module1.60 (GND), Module1.65 (GND), Module1.66 (GND), Module1.71 (GND), Module1.74 (GND), Module1.98 (GND), Module1.107 (GND), Module1.108 (GND), Module1.113 (GND), Module1.114 (GND), Module1.119 (GND), Module1.120 (GND), Module1.125 (GND), Module1.126 (GND), Module1.131 (GND), Module1.132 (GND), Module1.137 (GND), Module1.138 (GND), Module1.144 (GND), Module1.150 (GND), Module1.155 (GND), Module1.156 (GND), Module1.161 (GND), Module1.162 (GND), Module1.167 (GND), Module1.168 (GND), Module1.173 (GND), Module1.174 (GND), Module1.179 (GND), Module1.180 (GND), Module1.185 (GND), Module1.186 (GND), Module1.191 (GND), Module1.192 (GND), Module1.197 (GND), Module1.198 (GND), R4.2, R5.2, R12.2, R13.2, U1.3 (GND), U1.8 (GND), U2.3 (GND), U2.8 (GND), U3.19 (SHIELD), U3.20 (SHIELD), U6.19 (GND), U6.39 (GND), U7.1 (GND), U7.7 (GND), U7.9 (GND), U8.1 (GND/ADJ), U9.2 (GND)
unnamed: C1.1, U3.4 (CT), U3.5 (CT)
unnamed: D1.1 (K), R10.1
unnamed: D2.1 (K), R1.1
unnamed: D3.2 (A), U6.16 (PB2)
unnamed: D3.1 (K), R4.1
unnamed: D4.2 (A), U6.14 (PB0)
unnamed: D4.1 (K), R5.1
unnamed: J5.6, R14.2
unnamed: J7.1, U7.8 (OUT2)
unnamed: J7.6, U7.6 (OUT1)
unnamed: J11.2, SW1.2 (B)
unnamed: J15.1, U6.11 (PA5)
unnamed: J16.6, R8.2
unnamed: J18.1, U6.9 (PA3)
unnamed: J18.2, U6.8 (PA2)
unnamed: Module1.21 (LED_nACT), R1.2
unnamed: R3.1, U3.18 (LEDG_K)
unnamed: R2.1, U3.16 (LEDY_K)
unnamed: R9.1, R12.1, U6.10 (PA4)
unnamed: R13.1, U7.4 (ILIM)
PWR_BUT: J3.2, Module1.92 (PWR_BUT), U6.31 (B3)
Stm32 Serial RX: J8.8, J18.4, Module1.55 (GPIO14), U6.27 (A10)
Stm32 Serial TX: J8.10, J18.5, Module1.51 (GPIO15), U6.26 (A9)
nPWR_LED: Module1.95 (LED_nPWR), R10.2, U6.32 (B4)

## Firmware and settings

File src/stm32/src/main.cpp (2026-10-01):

#include <Arduino.h>
#include "Servo.h"  
#include <PID_v1.h>
#include <SPI.h>

#include <vl53l8cx.h>

// Encoder pins
#define interruptPinA PA0
#define interruptPinB PA1



Servo servo;
volatile long EncoderCount = 0;
int32_t EncoderCountFull = 0;

// Timer object for encoder
HardwareTimer *encoder;

// Timer object for PWM
HardwareTimer *pwm;

// Timer object for 100 Hz interrupt
HardwareTimer *tick100HzTimer;

int32_t impulse_diff = 0;

int32_t lastEncoderCount = 0;
int32_t rotations_per_sec = 0;

bool newdata = false, checkVoltage = false;

String strinList[100] = {};
int amountDividers = 0;


// PWM-capable pin for BlackPill F411.
// Avoid pins used by UART (often Serial1 = PA9/PA10 or PB6/PB7 depending on variant).
// Good alternatives include PA6/PA7 (TIM3), PB0/PB1 (TIM3), PB8/PB9 (TIM4).
#define PWM_PIN1 PA6
#define PWM_PIN2 PA7

#define SPI_CLK_PIN PB13
#define SPI_MISO_PIN PB14
#define SPI_MOSI_PIN PB15
#define CS_PIN1 PB10
#define CS_PIN2 PB1
#define CS_PIN3 PB7
#define CS_PIN4 PB6
// #define CS_PIN5 PA2
// #define CS_PIN6 PA3
#define LED2 PB0
#define LED1 PB2
#define BUTTON PA2
uint8_t status;
#define BUSSPEED 1500000

SPIClass DEV_SPI(SPI_MOSI_PIN, SPI_MISO_PIN, SPI_CLK_PIN);

VL53L8CX sensor_vl53l8cx_top1(&DEV_SPI, CS_PIN1, -1,  -1,  BUSSPEED);
VL53L8CX sensor_vl53l8cx_top2(&DEV_SPI, CS_PIN2, -1,  -1,  BUSSPEED);
VL53L8CX sensor_vl53l8cx_top3(&DEV_SPI, CS_PIN3, -1,  -1,  BUSSPEED);
VL53L8CX sensor_vl53l8cx_top4(&DEV_SPI, CS_PIN4, -1,  -1,  BUSSPEED);
// VL53L8CX sensor_vl53l8cx_top5(&DEV_SPI, CS_PIN5, -1,  -1,  BUSSPEED);
// VL53L8CX sensor_vl53l8cx_top6(&DEV_SPI, CS_PIN6, -1,  -1,  BUSSPEED);
int sensorCaptures[8] = {0,0,0,0,0,0,0,0};

int started = 0;
int ready = 0;


double Setpoint=0, Input, Output;
PID myPID(&Input, &Output, &Setpoint,0.5,20,0/*0.0005*/, DIRECT);

void setSpeed(double speed);
void motorController100Hz();
void waitForNewMessage();
void parse();

#define RESOLUTION VL53L8CX_RESOLUTION_8X8

/**
 * @brief Initialize and start continuous ranging on one VL53L8CX sensor.
 *
 * Runs begin()/init(), sets the 8x8 resolution, ranging frequency and
 * continuous mode, then starts ranging. Status is reported over Serial1.
 * @param sensor Pointer to the VL53L8CX instance to initialize.
 * @param speed  Ranging frequency in Hz.
 */
void initVL53(VL53L8CX * sensor, int speed)
{ 
  
  Serial1.println("Sensor Begin");
  // Configure VL53L8CX component.
  status = sensor->begin();
  Serial1.println("Sensor Init");
  status = sensor->init();
  if (status!=0)
  {
      Serial1.println("Sensor Init failed  ----------------");

  }
  else
  {
    Serial1.println("Sensor Init succeeded  **************");
    Serial1.println("Sensor resolution");
    status = sensor->set_resolution(RESOLUTION);
    Serial1.println("Sensor Frquency");
    sensor->set_ranging_frequency_hz(speed);
    Serial1.println("Sensor ranging mode");
    sensor->set_ranging_mode(VL53L8CX_RANGING_MODE_CONTINUOUS);
    Serial1.println("Sensor start ranging");
    status = sensor->start_ranging();
    Serial1.println("Sensor init Done");
  }


}

/**
 * @brief Poll a sensor and fetch a new ranging frame if one is ready.
 *
 * @param sensor Pointer to the VL53L8CX instance to read.
 * @param result Output buffer that receives the ranging data when available.
 * @return 1 if a new frame was copied into @p result, 0 otherwise.
 */
int update(VL53L8CX * sensor, VL53L8CX_ResultsData * result) 
{
  // Serial1.println("\nSensor updating");

  uint8_t NewDataReady = 0;
  // Serial1.println("looking for data");

  status = sensor->check_data_ready(&NewDataReady);
  if (status)
  {
    // Serial1.printf("-");
    return 0;
  }
  if (!NewDataReady)
  {
    // Serial1.printf(".");
    return 0;
  }

  // Serial1.printf("x");

  status = sensor->get_ranging_data(result);
  return 1;

}

/* Setup ---------------------------------------------------------------------*/
/**
 * @brief One-time hardware initialization run at power-up.
 *
 * Configures chip-select/LED/button pins, the UART link to the CM5, the
 * quadrature encoder (TIM2), the 100 Hz motor-control interrupt (TIM5), the
 * motor PWM outputs, the speed PID, the SPI bus and all four ToF sensors.
 */
void setup()
{
  pinMode(CS_PIN1, OUTPUT);
  digitalWrite(CS_PIN1,HIGH);
  pinMode(CS_PIN2, OUTPUT);
  digitalWrite(CS_PIN2,HIGH);
  pinMode(CS_PIN3, OUTPUT);
  digitalWrite(CS_PIN3,HIGH);
  pinMode(CS_PIN4, OUTPUT);
  digitalWrite(CS_PIN4,HIGH);
  // pinMode(CS_PIN5, OUTPUT);
  // digitalWrite(CS_PIN5,HIGH);
  // pinMode(CS_PIN6, OUTPUT);
  // digitalWrite(CS_PIN6,HIGH);
  pinMode(LED1, OUTPUT);
  pinMode(LED2, OUTPUT);
  pinMode(BUTTON, INPUT_PULLUP);
  digitalWrite(LED1, LOW);
  digitalWrite(LED2, LOW);

  Serial1.begin(921600);

  // while(1)
  // {
  //   bool pressed = digitalRead(BUTTON);
  //   Serial1.print("button,");
  //   Serial1.printf(" %01i \n",pressed);   // Button state  
  // }
    

  Serial1.println("Startup");
  pinMode(LED_BUILTIN, OUTPUT);
  pinMode(PA15, OUTPUT);
  pinMode(PA4, INPUT_ANALOG);
  // pinMode(LED1, OUTPUT);
  // pinMode(LED2, OUTPUT);
  // digitalWrite(LED1, HIGH);
  // digitalWrite(LED2, HIGH);


  // *** Hardware Encoder Setup (TIM2) ***
  encoder = new HardwareTimer(TIM2);
  
  // Encoder mode: count on rising edges only
  encoder->setMode(1, TIMER_INPUT_CAPTURE_RISING, interruptPinA);
  encoder->setMode(2, TIMER_INPUT_CAPTURE_RISING, interruptPinB);
  
  // Configure encoder mode via HAL
  TIM_Encoder_InitTypeDef encoderConfig;
  encoderConfig.EncoderMode = TIM_ENCODERMODE_TI12;
  encoderConfig.IC1Polarity = TIM_INPUTCHANNELPOLARITY_RISING;
  encoderConfig.IC1Selection = TIM_ICSELECTION_DIRECTTI;
  encoderConfig.IC1Prescaler = TIM_ICPSC_DIV1;
  encoderConfig.IC1Filter = 0;
  encoderConfig.IC2Polarity = TIM_INPUTCHANNELPOLARITY_RISING;
  encoderConfig.IC2Selection = TIM_ICSELECTION_DIRECTTI;
  encoderConfig.IC2Prescaler = TIM_ICPSC_DIV1;
  encoderConfig.IC2Filter = 0;
  
  HAL_TIM_Encoder_Init(encoder->getHandle(), &encoderConfig);
  
  // Set counter to max value for bidirectional counting
  encoder->setOverflow(0xFFFF);
  encoder->setCount(0); 
  
  HAL_TIM_Encoder_Start(encoder->getHandle(), TIM_CHANNEL_ALL);
  
  Serial1.println("Hardware encoder initialized");

  // 100 Hz interrupt (TIM5)
  tick100HzTimer = new HardwareTimer(TIM5);
  tick100HzTimer->setOverflow(100, HERTZ_FORMAT);
  tick100HzTimer->attachInterrupt(motorController100Hz);
  tick100HzTimer->resume();

  // Initialize PWM output: 70kHz with 20% duty cycle
  pinMode(PWM_PIN1, OUTPUT);
  pinMode(PWM_PIN2, OUTPUT);
  analogWriteResolution(10);                 // 0..255
  analogWriteFrequency(70000);              // 70 kHz (core-wide setting)

  setSpeed(0);

  Serial1.println("done");

  Input = 100;
  myPID.SetOutputLimits(-100, 100);
  myPID.SetSampleTime(1);
  myPID.SetMode(AUTOMATIC);

  // Initialize SPI bus.
  Serial1.println("Sensor init start");
  DEV_SPI.begin();
  delay(100);

  Serial1.println("***              CS1 ");
  initVL53(&sensor_vl53l8cx_top1,30);
  Serial1.println("***              CS2 ");
  initVL53(&sensor_vl53l8cx_top2,30);
  Serial1.println("***              CS3 ");
  initVL53(&sensor_vl53l8cx_top3,30);
  Serial1.println("***              CS4 ");
  initVL53(&sensor_vl53l8cx_top4,30);
  // Serial1.println("***              CS5 ");
  // initVL53(&sensor_vl53l8cx_top5,30);
  // Serial1.println("***              CS6 ");
  // initVL53(&sensor_vl53l8cx_top6,30);
 
  servo.attach(PA5);
}


/**
 * @brief Drive the motor H-bridge at a signed speed via PWM.
 *
 * Positive drives forward, negative reverse, zero applies an active brake
 * (both outputs high). The magnitude is clamped to +/-95%.
 * @param speed Signed speed percentage (-95..95).
 */
void setSpeed(double speed)
{
  if (speed > 0) 
  {
    speed = constrain(speed, 0, 95);
    analogWrite(PWM_PIN2, 0);
    analogWrite(PWM_PIN1, (1023*(speed/100.0)));
  } else if (speed < 0) 
  {
    speed = constrain(speed, -95, 0);
    analogWrite(PWM_PIN1, 0);
    analogWrite(PWM_PIN2, (1023*(abs(speed)/100.0)));
  } else 
  {
    // Both outputs high = active short brake (motor terminals tied together).
    analogWrite(PWM_PIN1, 1023);
    analogWrite(PWM_PIN2, 1023);
  }

  // analogWrite(PWM_PIN1, 200);
  // analogWrite(PWM_PIN2, 800);
}
/**
 * @brief Send one sensor's full ranging grid to the CM5 as a CSV line.
 *
 * Emits "cam,<id>,<v0>,...,<vN>,". Cells without a valid target status are
 * reported as -1.
 * @param cam    1-based sensor id written into the message.
 * @param result Ranging data to transmit.
 */
void printSensorData(int cam,VL53L8CX_ResultsData * result) 
{
  int res=8;
  if (RESOLUTION == VL53L8CX_RESOLUTION_4X4)
    res=4;
  Serial1.printf("cam,%i",cam);
  for (int i = 0; i < res*res; i++) 
  {
    // Status 5 and 9 are the VL53L8CX "valid measurement" codes; anything
    // else is unreliable and reported as -1.
    if (result->target_status[i]!=5 && result->target_status[i]!=9)
      Serial1.printf(",-1");
    else
      Serial1.printf(",%i", result->distance_mm[i]);
  }
  Serial1.println(",");
}

/**
 * @brief Send every 4th cell of a grid, starting at @p offset, as a CSV line.
 *
 * Used to split one sensor's grid across multiple smaller messages.
 * @param cam    Sensor id used to derive the reported id (offset+1).
 * @param result Ranging data to transmit.
 * @param offset Starting cell offset (0..3) selecting the interleaved subset.
 */
void printMultiSensorData(int cam,VL53L8CX_ResultsData * result,int offset) 
{
  int res=8;
  if (RESOLUTION == VL53L8CX_RESOLUTION_4X4)
    res=4;
  Serial1.printf("cam,%i",offset+1);
  for (int i = 0; i < res*res*4; i+=4) 
  {
    if (result->target_status[i+offset]!=5 && result->target_status[i+offset]!=9)
      Serial1.printf(",-1");
    else
      Serial1.printf(",%i", result->distance_mm[i+offset]);
  }
  Serial1.println(",");
}

/**
 * @brief Drain the UART RX buffer, splitting incoming bytes into tokens.
 *
 * Accumulates comma-separated fields into @c strinList and calls parse() when
 * a newline terminates a command.
 */
void waitForNewMessage()
{
  char str[2] = "";
  int r = Serial1.read();
  while (r>=0) 
  {
    if (r==',')
    {
      if (amountDividers<99)
        amountDividers++;
    }
    else if (r=='\n')
    {
      parse();
    }
    else
    {
      str[0]=(char)r;
      strinList[amountDividers] += String(str);
    }
    r = Serial1.read();
   
  }
// Serial1.printf(" %i:<%c> ",r,r);
}

/**
 * @brief Act on one fully received command from the CM5.
 *
 * Handles "speed", "servo", "checkVoltage", "ready" and "start" messages, then
 * clears the token buffer for the next command.
 */
void parse()
{
  if (strinList[0] == "speed" && amountDividers==1) 
  {
    Setpoint = strinList[1].toDouble();
  } 
  else if (strinList[0] == "servo" && amountDividers==1) 
  {
    servo.write(strinList[1].toDouble());
  }
  else if (strinList[0] == "checkVoltage" && amountDividers==1) 
  {
    checkVoltage = strinList[1].toInt()>0;
  }
  else if (strinList[0] == "ready" && amountDividers==1) 
  {
    ready = 1;
  }
  else if (strinList[0] == "start" && amountDividers==1) 
  {
    started = 1;
  }

  for (int i=0;i<=amountDividers;i++)
  {
    // Serial1.printf(" %i:<",i);
    // Serial1.print(strinList[i]);
    // Serial1.print("> ");
    strinList[i]="";
  }
  amountDividers=0;
  // Serial1.println("");
}


/**
 * @brief Main super-loop: handle serial I/O, sensors and status reporting.
 *
 * Reads incoming commands, measures battery voltage (shutting the motor down
 * and signaling the CM5 on sustained under-voltage), polls the ToF sensors
 * and streams their data, and periodically sends status and speed packets.
 */
void loop()
{
  waitForNewMessage();
  uint32_t ad = analogRead(PA4);
  double vBat=(double)ad * 3.3*5.7 / 1023.0;

  //Serial1.printf("Ad: %i V:<%i> \n",ad,(int)(vBat*10.));
  static unsigned long lastTime = 0;
  static bool ledState = false;

  // Serial1.println("Button: " + String(digitalRead(BUTTON)));
  if (started==0)
  {
    if (ready == 1)
    {
      bool pressed = digitalRead(BUTTON)==LOW;
      Serial1.print("button,");
      Serial1.printf("%01i",pressed);   // Button state
      Serial1.print(",\n");
      digitalWrite(LED1, HIGH);
      digitalWrite(LED2, LOW);
    } 
    else 
    {
      digitalWrite(LED1, LOW);
      digitalWrite(LED2, HIGH);
    }
  }
  static VL53L8CX_ResultsData results1;
  static VL53L8CX_ResultsData results2;
  static VL53L8CX_ResultsData results3;
  static VL53L8CX_ResultsData results4;
  // static VL53L8CX_ResultsData results5;
  // static VL53L8CX_ResultsData results6;

  int s1=0;
  int s2=0;
  int s3=0;
  int s4=0;
  int s5=0;
  int s6=0;

  static int d=0;
  d++;
  s1=update(&sensor_vl53l8cx_top1, &results1);
  // if (d%3==0)
    s2=update(&sensor_vl53l8cx_top2, &results2);
  // if ((d+1)%3==0)
    s3=update(&sensor_vl53l8cx_top3, &results3);
  // if ((d+2)%3==0)
    s4=update(&sensor_vl53l8cx_top4, &results4);
    // s5=update(&sensor_vl53l8cx_top5, &results5);
    // s6=update(&sensor_vl53l8cx_top6, &results6);
  if (s1>0)
    printSensorData(1,&results1);
  if (s2>0)
    printSensorData(2,&results2);
  if (s3>0)
    printSensorData(3,&results3);
  if (s4>0)
    printSensorData(4,&results4);
  // if (s5>0)
  //   printSensorData(5,&results5);
  // if (s6>0)
  //   printSensorData(6,&results6);

  // if (s3>0)
  // {
  //   printMultiSensorData(3,&results3,0);    
  //   printMultiSensorData(3,&results3,1);    
  //   printMultiSensorData(3,&results3,2);    
  //   printMultiSensorData(3,&results3,3);    
  // }
        
  sensorCaptures[0]+=s1;
  sensorCaptures[1]+=s2;
  sensorCaptures[2]+=s3;
  sensorCaptures[3]+=s4;
  sensorCaptures[4]+=s5;
  sensorCaptures[5]+=s6;

  static int c=0;
  static unsigned long lastPrint=micros();

  static int lowBatCounter=0;
  if (vBat<10.5)
  {
    // Require ~100 consecutive low readings before acting, so brief voltage
    // sags under load don't trigger a false shutdown.
    lowBatCounter++;
    if (lowBatCounter>100)
    {
      // Battery critically low: stop the motor and keep warning the CM5
      // (wiggling the servo as a visible alarm) until power is cut.
      while (true)
      {
        if (micros()-lastPrint>500000) {
          uint32_t ad = analogRead(PA4);
          double vBat=(double)ad * 3.3*5.7 / 1023.0;
          lastPrint=micros();
          Setpoint = 0;
          Serial1.print("lowVoltage,");
          Serial1.print(vBat);  //Voltage
          Serial1.print(",\n");
          static int pos=0;
          servo.write(90);
          if (pos==0)
            servo.write(60);
          if (pos==1)
            servo.write(90);
          if (pos==2)
            servo.write(120);
          if (pos==3)
            servo.write(90);      
          pos++;
          if (pos>3)
            pos=0;
        }
      }
    }
  }
  else
  {
    lowBatCounter--;
    if (lowBatCounter<0)
      lowBatCounter=0;  
  }


  if (micros()-lastPrint>500000)
  {

  
    lastPrint = micros();
    // Serial1.printf("%i    %i  %i     ",impulse_diff,rotations_per_sec,(int)(Output*10)); 
    Serial1.print("stat,");
    Serial1.print(vBat);    //Voltage
    for (int i=0;i<6;i++) 
    {
      Serial1.print(",");
      Serial1.print(sensorCaptures[i]*2);
      sensorCaptures[i]=0;
    }
    // uint8_t status;
    // sensor_vl53l8cx_top1.get_ranging_frequency_hz(&status);
    // Serial1.printf("Freq: %i ",status);

    Serial1.print(",\n");
  }

  if (newdata) 
  {
    // static double dir=1;
    // if (Setpoint>=200)
    //   dir=-1;
    // if (Setpoint<=40)
    //   dir=1;

    // Setpoint+=dir*2;    

    Serial1.print("speed,");
    Serial1.printf("%05i",rotations_per_sec);   //Speed
    Serial1.print(",");
    Serial1.printf("%05i",EncoderCountFull);    //Counter
    Serial1.print(",");
    Serial1.printf("%03i",(int)Output);    //Counter
    Serial1.print(",");    
    Serial1.printf("%03i",(int)Setpoint);    //Counter
    Serial1.print(",\n");
    newdata = false;
  }
}

// Cams 1/2/3/4/5/6:
// Cam,1/2/3/4/5/6,value1,value2,...,value16/64;

// Speed,Counter,Voltage:
// speed,value,value,value;


/**
 * @brief 100 Hz timer ISR running the closed-loop speed controller.
 *
 * Reads the encoder delta, converts it to rotations/second, feeds the PID
 * controller and updates the motor PWM. Flags @c newdata so loop() can report
 * the latest speed. PA15 is toggled to mark the ISR duration.
 */
void motorController100Hz()
{
  digitalWrite(PA15,1); 
  // Read encoder count from hardware timer
  EncoderCount = (long)encoder->getCount();
  
  
  // Calculate impulses per second
  impulse_diff = EncoderCount - lastEncoderCount;
  // Handle the 16-bit timer wrapping around 0/0xFFFF in either direction.
  if (impulse_diff > 30000)
    impulse_diff-=0xffff;
  if (impulse_diff <- 30000)
    impulse_diff+=0xffff;

  int32_t impulses_per_sec = impulse_diff * 100;   // sampled at 100 Hz

  EncoderCountFull += impulse_diff;
  

  //  30 counts per rotation
  rotations_per_sec = impulses_per_sec / 30.0;
  int32_t rpm = impulses_per_sec * 60.0 /30;

  Input = (double)rotations_per_sec;

  myPID.Compute();
  if (Setpoint==0)
  {
    // Hard stop: zero output and reset the PID so it doesn't wind up at idle.
    Output=0;
    myPID.Initialize();
  }
    
  
  setSpeed(Output);
  lastEncoderCount = EncoderCount;  
  digitalWrite(PA15,0); 

  newdata = true;
}

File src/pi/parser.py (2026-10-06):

import serial # type: ignore
import subprocess
import time
import math
import board # type: ignore
import busio # type: ignore
import adafruit_bno055 # type: ignore
from glob import glob
from subprocess import call
from gyro85 import gyroBNO085


class Parser:
    """@brief Shared data model and serial bridge between CM5 and STM32.

    Holds the latest sensor readings (ToF grids, speed, heading, voltage),
    runs the serial read loop in `pars()`, exposes helpers to send drive
    commands to the STM32, and tracks the detected obstacle layout.
    """
    RED = 0
    GREEN = 1
    
    amountSensors = 6
    leftSensor = 0      # 0
    frontSensor = 1     
    rightSensor = 2
    backSensor = 3
    angleRightSensor = 4
    angleLeftSensor = 5
    CW = 0
    CCW = 1
    Default = 0
    Capture_1_Only = 1
    Capture_Dynamic = 2
    All = 0
    HSV = 1
    
    def __init__(self):
        """@brief Initialize shared state, the gyro and the serial port.

        Sets up the per-sensor ToF buffers, waits for gyro calibration and
        opens the UART to the STM32 at 921600 baud.
        @return None
        """
        for i in range(self.amountSensors):
            self.getPosForCam(i, setSensorIndex=True)

        self.camValues = []
        self.camValues = [[0 for _ in range(64)] for _ in range(self.amountSensors)]
        self.sensorCaptures = [0 for _ in range(self.amountSensors)]
        self.rps = 0
        self.count = 0
        self.output = 0
        self.setpoint = 0
        self.voltage = 12.6
        self.speed = 0
        self.distance = 0
        self.time = 0
        self.startTime = time.time()
        self.endTime = 0
        self.uiType = Parser.Default
        self.obstacles = []
        self.currentCommand = ""
        self.obstacles = [None for _ in range(12)]
        self.lastHeading = 0
        self.heading = 0
        self.round = 0
        self.Direction = Parser.CW
        self.button = False
        self.started = False


        # self.i2c = busio.I2C(board.SCL, board.SDA)
        # self.gyro = adafruit_bno055.BNO055_I2C(self.i2c, address=0x28)
        self.gyro85 = gyroBNO085()

        while not self.calibDone():
            print("Waiting for gyro calibration:", self.gyro.calibration_status)
            time.sleep(0.5)


        self.ser = serial.Serial()
        self.ser.port = "/dev/ttyAMA0"
        self.ser.baudrate = 921600
        self.ser.bytesize = 8
        self.ser.stopbits = serial.STOPBITS_ONE
        self.ser.parity = serial.PARITY_NONE
        self.ser.open()
        
        self.imageType = Parser.All
        self.currentImage = 0
        self.images = sorted(glob("capture/*.jpg"))         # get all files in captureStore ending with .jpg
        self.hsvImages = sorted(glob("capture/*hsv.jpg"))   # get all files in captureStore ending with hsv.jpg

    def loadImages(self):
        """@brief Refresh the cached lists of captured images for the UI viewer.

        @return None
        """
        self.images = sorted(glob("capture/*.jpg"))         # get all files in captureStore ending with .jpg
        self.hsvImages = sorted(glob("capture/*hsv.jpg"))   # get all files in captureStore ending with hsv.jpg

    def calibDone(self):
        """@brief Report whether the gyro reports a usable calibration state.

        @return bool True when calibration is complete (currently always True).
        """
        return True
        # _, gyroCalibration, _, magnetometerCalibration = self.gyro.calibration_status
        # return gyroCalibration == 3

    def getHeading(self):
        """@brief Return the current heading in degrees from the BNO085 gyro.

        Applies a small per-lap correction offset that compensates for the
        gyro drifting slightly more to one side depending on drive direction.
        @return float heading angle in degrees.
        """
        # return self.gyro85.get_heading()
    
        # if not hasattr(self, 'gyro') or self.gyro is None:
        #     return 0
        
        # angle = self.gyro.euler[0]
        angle = self.gyro85.get_heading()
        
        if angle is None:
            angle = 0
        
        # Per-lap drift compensation: the gyro accumulates a small bias each
        # lap, so nudge the heading a little further every round.
        if self.Direction == self.CCW:
            if self.round == 0:
                angle += 0
            elif self.round == 1:
                angle += -1
            elif self.round == 2:
                angle += -1.5                     # kleinere Zahl (mehr negativ)  = er steuer mehr nach rechts
        else:
            if self.round == 0:
                angle += 0
            elif self.round == 1:
                angle += 1
            elif self.round == 2:
                angle += 2
        
        return angle
        newHeading = self.gyro.euler[0]
        diff=newHeading - self.lastHeading
        if diff < -300:
            diff += 360
        elif diff > 300:
            diff -= 360

        cal=1.00 #1.0041667 # calibration factor to match the heading with the real rotation of the robot. (360/358.5)
                            # was calculated by comparing the gyro heading with the actual rotation of the robot. 
                            # The robot was rotated 10 times and the average difference between the gyro heading and the
                            # actual rotation was calculated to be 1.5 degrees per 360 degrees of rotation. This factor is used to correct the heading calculation.

        # if (diff>0):
        #     diff *= cal
        # else:
        #     diff /= cal

        diff *= cal     # the gyro turns not enough in  both directions, so the factor is applied to both positive and negative differences.

        self.heading += diff
        if (self.heading < 0):
            self.heading += 360 
        elif (self.heading >= 360):
            self.heading -= 360
        self.lastHeading = newHeading

        return self.heading
    def resetGyro(self):
        """@brief Zero the gyro heading so the current orientation becomes 0°.

        @return None
        """
        self.gyro85.reset_heading()
        # del self.gyro
        # self.lastHeading = 0
        # self.heading=0
        # self.gyro = adafruit_bno055.BNO055_I2C(self.i2c, address=0x28)
        # self.gyro.mode = adafruit_bno055.IMUPLUS_MODE
        # while not self.calibDone():
        #     print("Waiting for gyro calibration:", self.gyro.calibration_status)
        #     time.sleep(0.1)
        
    def sendReadySignal(self):
        """@brief Tell the STM32 the CM5 is initialized and ready to start.

        @return None
        """
        self.send("ready,1\n")

    def sendStartSignal(self):
        """@brief Tell the STM32 the run has started (e.g. button pressed).

        @return None
        """
        self.send("start,1\n")
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

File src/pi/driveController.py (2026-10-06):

import time
import traceback

from parser import Parser
from logger import Logger
from subprocess import call

class DriveController:
    """High-level motion helper for heading, speed, and wall-relative maneuvers."""

    logCountetr = 0
    
    backWall = 4
    rightWall = 5
    frontWall = 1
    leftWall = 3
    angleLeftWall = 0
    angleRightWall = 2
    auto = 0
    turnRight = 1
    turnLeft = 2
    smallest = 0
    biggest = 1
    firstEnd = 0
    
    
    def __init__(self, parser: Parser, stop_event, logger: Logger = None):
        """Initialize controller state and bind it to the live parser sensors and logger."""
        DriveController.angleLeftWall = parser.angleLeftSensor
        DriveController.angleRightWall = parser.angleRightSensor
        DriveController.frontWall = parser.frontSensor
        DriveController.rightWall = parser.rightSensor
        DriveController.leftWall = parser.leftSensor
        DriveController.backWall = parser.backSensor
        
        self.defaultTopSpeed = 1.8
        self.topSpeed = self.defaultTopSpeed
        self.acceleration = 3
        self.deacceleration = 8
        self.setpoint = 0
        self.targetSpeed = 0
        self.targetHeading = 0
        self.lastTime = 0
        self.section = 0
        self.turnDir = self.auto
        self.parser = parser
        self.stop_event = stop_event
        self.pidSteer = PIDController(Kp=1, Ki=0, Kd=0, setpoint=0, min=-90, max=90)
        self.pidSteer2 = PIDController(Kp=0.5, Ki=0, Kd=0, setpoint=0, min=-90, max=90)
        self.logger = logger if logger is not None else Logger()
        self.resetAvoidWall()
        
    def end(self):
        """Stop the vehicle and report whether the external stop event requested shutdown."""
        if self.stop_event.is_set():
            self.parser.setSpeed(0)
            self.parser.setSteer(90)
            if self.parser.endTime == 0:
                self.parser.endTime = time.time()
            if DriveController.firstEnd == 0:
                call("sudo systemctl restart smbd", shell=True)
                DriveController.firstEnd = 1
            return True
        return False
    
    # start helper functions:
    
    def convertDir(self, parser: Parser, dir):
        """@brief Mirror a wall/sensor direction when driving clockwise.

        Left/right (and angled) walls swap when the course is run CW so the
        same high-level logic works for both directions; CCW is unchanged.
        @param parser Parser holding the current drive direction.
        @param dir    the wall/sensor constant to convert.
        @return the mirrored wall constant for CW, or `dir` unchanged for CCW.
        """
        convertDic = {
            self.angleLeftWall: self.angleRightWall,
            self.angleRightWall: self.angleLeftWall,
            self.leftWall: self.rightWall,
            self.rightWall: self.leftWall,
            self.frontWall: self.backWall,
            self.backWall: self.frontWall,
        }
        if parser.Direction == parser.CW:
            return convertDic[dir]
        else:
            return dir
    
    def getDist(self, poses:list, row = 3, wallDir = frontWall, mode = biggest):
        """Return the selected distance sample from one camera row across the given column indices."""
        val = 0
        tempVal = 0
        row = 3
        for i in poses:
            tempVal = self.parser.camValues[wallDir][i+row*8]
            if mode == self.biggest and tempVal > val:
                val = tempVal
            elif mode == self.smallest and tempVal < val and tempVal > 0:
                val = tempVal
        return val

    def wallToString(self, wall):
        """@brief Return a human-readable name for a wall/sensor constant.

        @param wall the wall constant (front/right/left/back/angled).
        @return str descriptive wall name, or "unknown wall".
        """
        if wall == self.frontWall:
            return "front wall"
        elif wall == self.rightWall:
            return "right wall"
        elif wall == self.leftWall:
            return "left wall"
        elif wall == self.backWall:
            return "back wall"
        elif wall == self.angleLeftWall:
            return "angle left wall"
        elif wall == self.angleRightWall:
            return "angle right wall"
        else:
            return "unknown wall"

    def nextSection(self):
        """Return the next course section index, wrapping from section 3 back to 0."""
        if self.section < 3:
            return self.section+1
        else:
            return 0
    
    def prevSection(self):
        """Return the previous course section index, wrapping from section 0 back to 3."""
        if self.section > 0:
            return self.section-1
        else:
            return 3
    
    def setCommand(self, command):
        """Store the current high-level maneuver name on the parser for status reporting."""
        self.parser.currentCommand = f"{command} @{self.logger.lineCount}"
        
    
    def setSpeed(self, speed):
        """Update the target drive speed that `calcAccel` ramps toward."""
        self.targetSpeed = speed
    
    def setTargetHeading(self, heading):
        """Normalize a heading into the current section and clamp it to [-180, 180]."""
        
        # Headings are given relative to the section; rotate them into the
        # global gyro frame (and flip sign for CW so both directions match).
        if self.parser.Direction == self.parser.CW:      # rotating to match current section
            heading = -heading + self.section*90   
        else:
            heading += self.section*-90       
        
        while heading > 180:
            heading -= 360
        while heading < -180:
            heading += 360
        self.targetHeading = heading
    
    def logStuff(self, message):
        """@brief Log a message annotated with the current section and run time.

        @param message str text to record.
        @return None
        """
        self.logger.log(f"{message}, Section: {self.section}, Time: {time.time()-self.parser.startTime:.2f}")
    
    def logCaller(self):
        """@brief Log which external function called the current driving primitive.
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

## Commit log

2026-02-17 Add Baseboard Kicad project
    [CM5_GPIO.kicad_sch, CM5_HighSpeed.kicad_sch, PCIe-M2.kicad_sch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]
2026-02-19 Baseboard partial routing
    [CM5_HighSpeed.kicad_sch, baseboard.kicad_pcb, baseboard.kicad_sch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]
2026-02-20 Finish PCB routing
    [CM5_GPIO.kicad_sch, CM5_HighSpeed.kicad_sch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]
2026-02-20 Setup baseboard pcb production settings
    [CM5_GPIO.kicad_sch, baseboard.kicad_pcb, stm32.kicad_sch]
2026-02-21 Last production adjustments
    [WroBB26_bom.csv, WroBB26_designators.csv, WroBB26_positions.csv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]
2026-03-12 Correct V1 mistakes : Turned MISO, Correct STM32 template. Add BMO055 Gyroskope . Add servo connector. Add serial port connector. Add Pi - Stm32 serial connection. Add Silkscreen texts.
    [CM5_GPIO.kicad_sch, CM5_HighSpeed.kicad_sch, Lowderdeck.stl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]
2026-03-12 Add V2 production files
    [WroBB26V2_bom.csv, WroBB26V2_designators.csv, WroBB26V2_positions.csv]
2026-03-24 Tune pid controller, expand communication protocol
2026-03-31 Add command parsing to stm32
2026-03-31 Pi tof camera parsing and basic ui display
2026-04-02 Implement PID controller for steering and enhance drive controller functionality
2026-04-06 Add configuration files for PlatformIO and update main.cpp for sensor initialization
2026-04-10 Add camera module for color-based obstacle detection and integrate with drive controller, add first obsta le avoidance test
    [camera.py, driveController.py, main.py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]
2026-04-23 -Enhance camera and drive controller functionality for obstacle detection and navigation - Modified DriveController to include new methods for setting commands and adjusting speed and heading. - Impr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
2026-04-28 add tof-sensor 5 and 6, advance obstacle course
2026-05-07 added Camera Testing function, added obstacle Challenge Single
2026-05-09 bugfix and update gitignore
    [main.py]
2026-05-11 Refactor camera and drive controller for improved obstacle detection and logging; update .gitignore and UI display
2026-05-13 Added independent monitor for temperature and runtime
2026-05-13 Refactor gyro handling and logging; update wall drive logic and UI display
2026-05-13 Add gyro rate calibration
2026-05-13 Enhance sensor initialization and add support for additional sensors in main.cpp
2026-05-13 Reduce SPI busspeed and sensor update rate to prevent sensor dropouts
    [main.cpp]
2026-05-15 - Enhanced `DriveController` with improved heading normalization and added `tightTurn` method for better maneuverability. - Introduced `gyroBNO085` class for interfacing with the BNO085 IMU, - Update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
    [cameraAIO.py, driveController.py, gyro85.py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]
2026-05-16 Disable physically damaged sensors
    [main.cpp]
2026-05-17 Add button to start driving
2026-05-25 Refine obstacle detection and navigation logic in camera and gyro modules
2026-05-31 Enhance logging for color detection and obstacle avoidance in singleScanClockwise and parkCW functions
    [obstacleChallengeSingle.py]
2026-06-02 Refactor camera for easyer calibration Improve parking add scanClockwiseSimulation function
2026-06-13 Enhanced local color detection calibration

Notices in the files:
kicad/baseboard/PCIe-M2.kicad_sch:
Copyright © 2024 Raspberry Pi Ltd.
